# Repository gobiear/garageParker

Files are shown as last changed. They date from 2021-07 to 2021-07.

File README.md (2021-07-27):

# garageParker
7/27/2021:
-added stl to hold rpi on wall with camera attached. very specific to my use case.

7/25/2021:
-Sumary: Simple brakets made to hold continuous motion servos to ceiling and simple "spools" made to hold fishing line to raise and lower indicator. Deployed and working in garage now

it vwerks:
https://youtu.be/HpaDFQKyFYE

7/18/2021:
-Summary: problems encountered with imageai model on pi4

- had to completely rebuild/retrain the model as the .m5 model that is output from imageai would not run on tflite on the raspberry pi when converting the imageai model to the tflite model using the provided function.

- Retraining the model locally was not possible as for what ever reason cannot get tflite_model_maker to install. Took short cut path and moved the training to google cloud https://console.cloud.google.com/

- Was pretty simple, uploaded the training images to a cloud container. Converted the PascalVOC.xml label files into csv format
- -- changes x/y cords to relative percent location [0-1] instead of size and pixel location easy to convert
- paid to train model on google over night( i think its like you get 300$ free at first so was free)
- the model was successful and is now successfully running on the pi4 recognizing tail lights from a screen. Need to move to garage to test if it works on actual car

check if im backing up and deploy parking aid 

Summary: Use/train imageai to detect my taillights when the backup light is on. When on just needs to send on signal to device to deploy parking aid. Should only work with tail lights in reverse. Should only be my tail lights not others. Should fail off, or on failure parking aid is not deployed.

Parking aid:
It must not obstruct or exist permenantly in the useable garage space. It needs to locate in two planes(x,y).
I thought some on this and to be honest the cheapest/simplest best solution is just some water proof tape on the floor to line up with backup cam lines. But that would not be much fun. Thought about also maybe some sort of laser line emiting light. Probably can be issue since height of ceiling relative to height of car may cut of critical angle of these lights for compact unit, might not though. Also thinking about just a simple motor/stepper with a ball on a string, when on deploys ball. When off retracts ball. 
Parking aid can be seperate from tail light recognition.

Tail light recognition:
Imageai need to download, annotate, train it to recognize my taillights with the reverse lights on. 

Training:
Training to detect my tail lights and my tail lights in reverse, infront of my garage. Because of this just used small training data i could gather my self. 
Took video of my car pulling in and out of the garage forward and reverse. Labeled the images tl for tail light and tlr for taillight reverse. 
ffmpeg video into frames and labeled the frames. 
I think since i just need it to know tail light reverse for my garage and use case it will be fine.
Trained over night and it appears to be working.

-Issues: 
7/25: Currently the "spool" is not great and line can stack up on winding up which will cause it to "overflow" the spool and drop a loop effectivly changing the height.
7/25: continous motion servos have no feed back and their position and rotation can not be accuratly determined, only you can set duty cycle for a period of time and derive what the distance travelled would be. This causes some issues as there is a difference between the force required to lower the object and the force required to lower the object, which will change the position. It may not be an issue for this specific use case but we shall see.

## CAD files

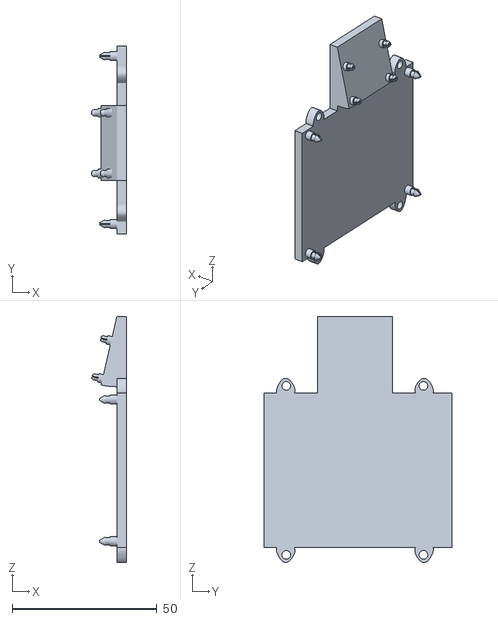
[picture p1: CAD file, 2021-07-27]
3d/piWallHolder.stl
12.0 x 64.9 x 85.0

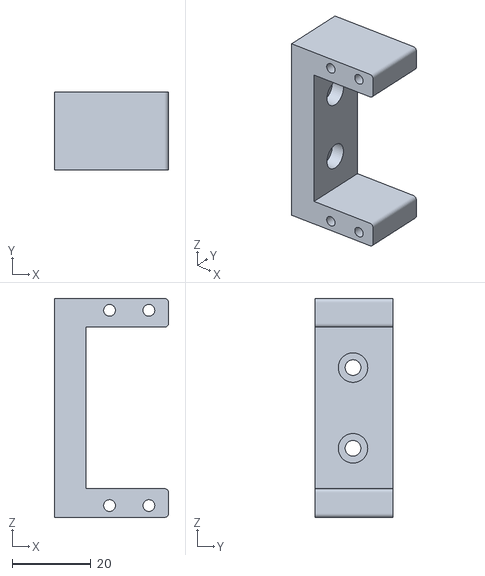
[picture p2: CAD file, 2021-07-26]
3d/servoHolder.stl
29.0 x 19.8 x 55.6

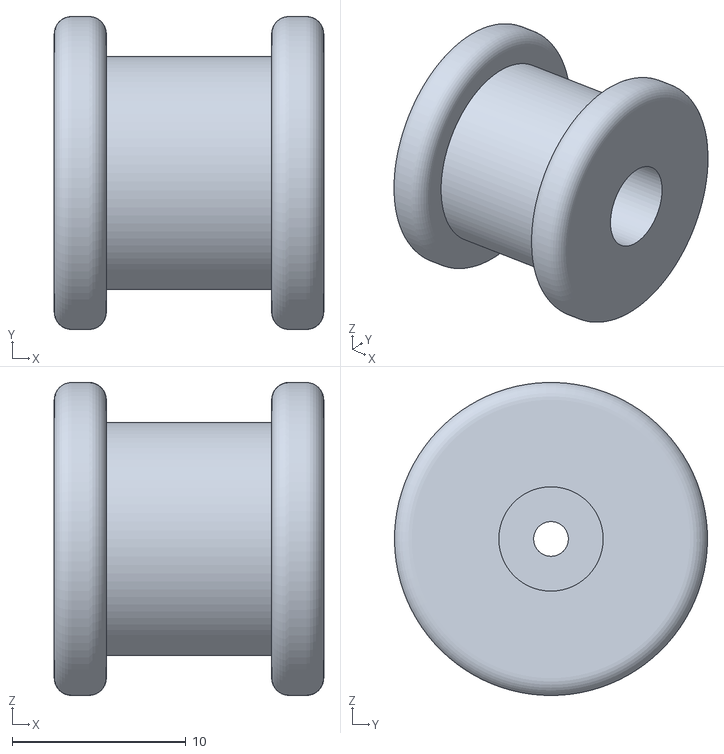
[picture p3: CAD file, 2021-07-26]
3d/tinySpool.stl
15.5 x 18.0 x 18.0

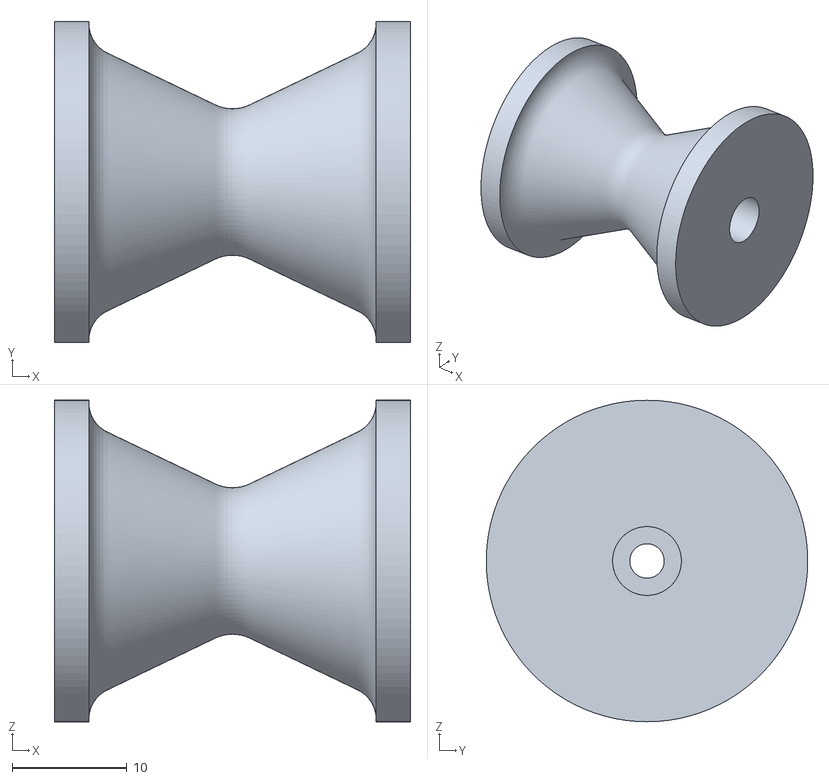
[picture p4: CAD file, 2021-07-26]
3d/spoool.stl
31.0 x 28.0 x 28.0

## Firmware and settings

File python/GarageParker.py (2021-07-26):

# code to get tflite running a model on raspberry pi source from
#https://github.com/EdjeElectronics/TensorFlow-Lite-Object-Detection-on-Android-and-Raspberry-Pi/blob/master/TFLite_detection_stream.py
#
#
import os
import argparse
import cv2
import numpy as np
import sys
import time
from threading import Thread
import importlib.util
import GarageServo
import GarageServoController
import time
from datetime import datetime

class VideoStream:
    """Camera object that controls video streaming from the Picamera"""

    def __init__(self, resolution=(640, 480), framerate=30):
        self.stream = cv2.VideoCapture(0)
        self.stream.set(cv2.CAP_PROP_EXPOSURE, -1)
        ret = self.stream.set(cv2.CAP_PROP_FOURCC, cv2.VideoWriter_fourcc(*'MJPG'))
        ret = self.stream.set(3, resolution[0])
        ret = self.stream.set(4, resolution[1])

        (self.grabbed, self.frame) = self.stream.read()

        self.stopped = False

    def start(self):
        Thread(target=self.update, args=()).start()
        return self

    def update(self):
        while True:
            if self.stopped:
                self.stream.release()
                return
            (self.grabbed, self.frame) = self.stream.read()

    def read(self):
        return self.frame

    def stop(self):
        self.stopped = True


# Define and parse input arguments
parser = argparse.ArgumentParser()
parser.add_argument('--modeldir', help='Folder the .tflite file is located in',
                    required=True)

args = parser.parse_args()

MODEL_NAME = args.modeldir
GRAPH_NAME = args.graph
LABELMAP_NAME = args.labels
min_conf_threshold = float(args.threshold)
resW, resH = args.resolution.split('x')
imW, imH = int(resW), int(resH)
use_TPU = args.edgetpu

from tflite_runtime.interpreter import Interpreter

CWD_PATH = os.getcwd()

PATH_TO_CKPT = os.path.join(CWD_PATH, MODEL_NAME, GRAPH_NAME)

PATH_TO_LABELS = os.path.join(CWD_PATH, MODEL_NAME, LABELMAP_NAME)

with open(PATH_TO_LABELS, 'r') as f:
    labels = [line.strip() for line in f.readlines()]

if labels[0] == '???':
    del (labels[0])

interpreter = Interpreter(model_path=PATH_TO_CKPT)

interpreter.allocate_tensors()

# Get model details
input_details = interpreter.get_input_details()
output_details = interpreter.get_output_details()
height = input_details[0]['shape'][1]
width = input_details[0]['shape'][2]

floating_model = (input_details[0]['dtype'] == np.float32)

input_mean = 127.5
input_std = 127.5

frame_rate_calc = 1
freq = cv2.getTickFrequency()

videostream = VideoStream(resolution=(imW, imH), framerate=30).start()
time.sleep(1)

servos = []
servo1 = GarageServo.GarageServo(0, 10, 0, 7.9)
servo2 = GarageServo.GarageServo(0, 11, 1, 7.95)

servos.append(servo1)
servos.append(servo2)

servo_controller = GarageServoController.GarageServoController(servos)

tlr_cnt = 0
deployed = False

last_tlr_seen = datetime.now()
while True:

    # Start timer (for calculating frame rate)
    t1 = cv2.getTickCount()


    # Grab frame from video stream
    frame1 = videostream.read()

    # Acquire frame and resize to expected shape [1xHxWx3]
    frame = frame1.copy()
    frame_rgb = cv2.cvtColor(frame, cv2.COLOR_BGR2RGB)
    frame_resized = cv2.resize(frame_rgb, (width, height))
    input_data = np.expand_dims(frame_resized, axis=0)

    # Normalize pixel values if using a floating model (i.e. if model is non-quantized)
    if floating_model:
        input_data = (np.float32(input_data) - input_mean) / input_std

    # Perform the actual detection by running the model with the image as input
    interpreter.set_tensor(input_details[0]['index'], input_data)
    interpreter.invoke()

    # Retrieve detection results
    boxes = interpreter.get_tensor(output_details[0]['index'])[0]  # Bounding box coordinates of detected objects
    classes = interpreter.get_tensor(output_details[1]['index'])[0]  # Class index of detected objects
    scores = interpreter.get_tensor(output_details[2]['index'])[0]  # Confidence of detected objects
    # num = interpreter.get_tensor(output_details[3]['index'])[0]  # Total number of detected objects (inaccurate and not needed)

    # Loop over all detections and draw detection box if confidence is above minimum threshold
    for i in range(len(scores)):
        if ((scores[i] > min_conf_threshold) and (scores[i] <= 1.0)):
            # Get bounding box coordinates and draw box
            # Interpreter can return coordinates that are outside of image dimensions, need to force them to be within image using max() and min()
            ymin = int(max(1, (boxes[i][0] * imH)))
            xmin = int(max(1, (boxes[i][1] * imW)))
            ymax = int(min(imH, (boxes[i][2] * imH)))
            xmax = int(min(imW, (boxes[i][3] * imW)))

            cv2.rectangle(frame, (xmin, ymin), (xmax, ymax), (10, 255, 0), 2)

            # Draw label
            object_name = labels[int(classes[i])]  # Look up object name from "labels" array using class index
            label = '%s: %d%%' % (object_name, int(scores[i] * 100))  # Example: 'person: 72%'
            labelSize, baseLine = cv2.getTextSize(label, cv2.FONT_HERSHEY_SIMPLEX, 0.7, 2)  # Get font size
            label_ymin = max(ymin, labelSize[1] + 10)  # Make sure not to draw label too close to top of window
            cv2.rectangle(frame, (xmin, label_ymin - labelSize[1] - 10),
                          (xmin + labelSize[0], label_ymin + baseLine - 10), (255, 255, 255),
                          cv2.FILLED)  # Draw white box to put label text in
            cv2.putText(frame, label, (xmin, label_ymin - 7), cv2.FONT_HERSHEY_SIMPLEX, 0.7, (0, 0, 0),
                        2)  # Draw label text

            if object_name == "tlr" and not deployed:
                tlr_cnt = tlr_cnt + 1

            if tlr_cnt == 10:
                tlr_cnt = 0
                servo_controller.mov_to_park_pos()
                deployed = True

            if deployed and object_name == "tlr":
                last_tlr_seen = datetime.now()

    duration = datetime.now() - last_tlr_seen
    duration_in_sec = duration.total_seconds()
    if deployed and duration_in_sec > 15 and 'tlr' not in classes:
        servo_controller.move_to_home()
        deployed = False

    # Draw framerate in corner of frame
    cv2.putText(frame, 'FPS: {0:.2f}'.format(frame_rate_calc), (30, 50), cv2.FONT_HERSHEY_SIMPLEX, 1, (255, 255, 0), 2,
                cv2.LINE_AA)
    cv2.putText(frame, 'Deployed: {0:.2f}'.format(deployed), (30, 75), cv2.FONT_HERSHEY_SIMPLEX, 1, (255, 255, 0), 2,
                cv2.LINE_AA)
    cv2.putText(frame, 'tlr_cnt: {0:.2f}'.format(tlr_cnt), (30, 100), cv2.FONT_HERSHEY_SIMPLEX, 1, (255, 255, 0), 2,
                cv2.LINE_AA)

    # All the results have been drawn on the frame, so it's time to display it.
    cv2.imshow('Object detector', frame)

    # Calculate framerate
    t2 = cv2.getTickCount()
    time1 = (t2 - t1) / freq
    frame_rate_calc = 1 / time1

    # Press 'q' to quit
    if cv2.waitKey(1) == ord('q'):
        break
    if cv2.waitKey(1) == ord('c'):
        servo_controller.calibrate_park_pos()

# Clean up
cv2.destroyAllWindows()
videostream.stop()

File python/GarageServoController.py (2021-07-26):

import GarageServo
import pi_servo_hat
import time
import sys


class GarageServoController:

    servos = [GarageServo]
    servo_hat = pi_servo_hat.PiServoHat()
    servo_hat.restart()
    servo_hat.set_pwm_frequency(50)

    def __init__(self, servos):
        self.servos = sorted(servos, key=lambda x: x.park_pos)

    def mov_to_park_pos(self):
        for servo in self.servos:
            self.servo_hat.set_duty_cycle(servo.channel, servo.up_dc)
            time.sleep(.001)

        last_sleep = 0
        for servo in self.servos:
            min_sleep = servo.park_pos - last_sleep
            for i in range(0, min_sleep):
                time.sleep(1)
            self.servo_hat.set_duty_cycle(servo.channel, servo.stop_dc)
            last_sleep = servo.park_pos

        self.servo_hat.restart()


    def move_to_home(self):
        for servo in self.servos:
            self.servo_hat.set_duty_cycle(servo.channel, servo.down_dc)
            time.sleep(.001)

        last_sleep = 0
        for servo in self.servos:
            min_sleep = servo.park_pos - last_sleep
            for i in range(0, min_sleep):
                #offset to account for more force required for up than down. shit
                time.sleep(1.03)
            self.servo_hat.set_duty_cycle(servo.channel, servo.stop_dc)
            last_sleep = servo.park_pos

        self.servo_hat.restart()

    #WIP
    def calibrate_park_pos(self):

        servo_index_to_cal = input("Enter index of servo to calibrate:")

        for servo in self.servos:
            if servo.channel == servo_index_to_cal:
                break
        else:
            print("Servo with index not found")

        servo_to_cal = servo

        input("Begin calibration upon hitting enter, press enter to stop")
        self.servo_hat.set_duty_cycle(servo_to_cal.channel, servo_to_cal.up_dc)
        sleep = 0

        while True:
            try:
                stdin = sys.stdin.read()
                if "\n" in stdin or "\r" in stdin:
                    break
            except IOError:
                pass
            time.sleep(.2)
            sleep = sleep + .2
            self.servo_hat.restart()

        while True:
            fine_adj = float(input("Enter fine adjustment or type ok to finish"))
            if fine_adj < 0:
                self.servo_hat.set_duty_cycle(servo.channel, servo_to_cal.down_dc)
            else:
                self.servo_hat.set_duty_cycle(servo.channel, servo_to_cal.up_dc)

            sleep = sleep + fine_adj
            try:
                stdin = sys.stdin.read()
                if "ok" in stdin:
                    break
            except IOError:
                pass
            time.sleep(fine_adj)
            self.servo_hat.restart()

        cnt = 0
        for servo in self.servos:
            if servo.channel == servo_index_to_cal:
                self.servos[cnt].set_park_pos(sleep)
                break
            cnt = cnt + 1

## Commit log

2021-07-26 base working version
    [servoHolder.stl, spoool.stl, tinySpool.stl]
2021-07-27 stl file for thing that can hold pi to wall with camera so its not a mess
    [piWallHolder.stl]
